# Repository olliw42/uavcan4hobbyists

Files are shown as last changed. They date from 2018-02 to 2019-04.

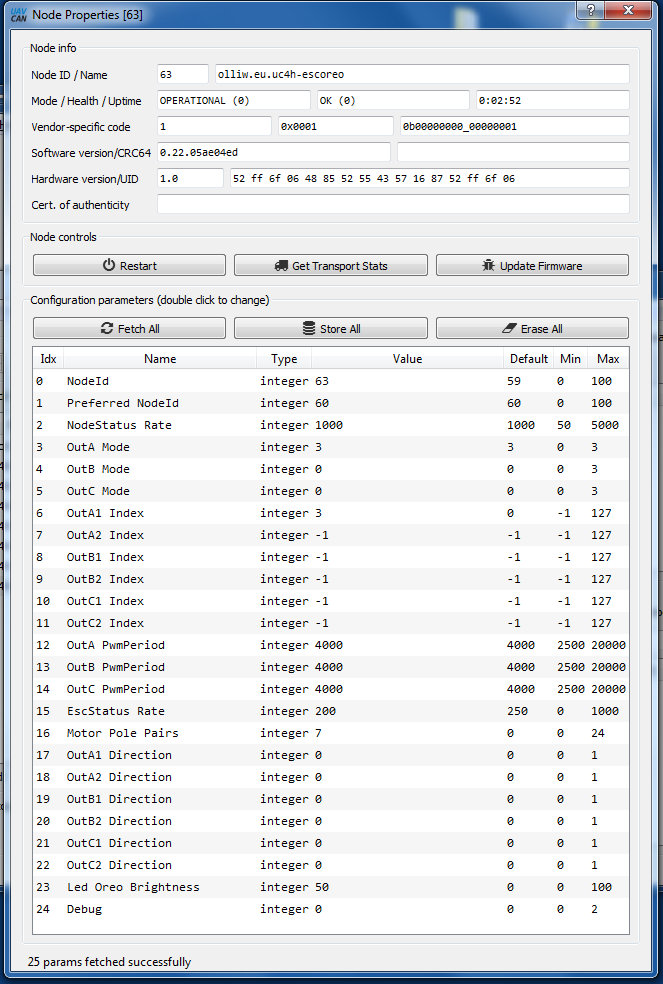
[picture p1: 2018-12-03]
olliws-parameters/olliws-20181203-esc-4.jpg

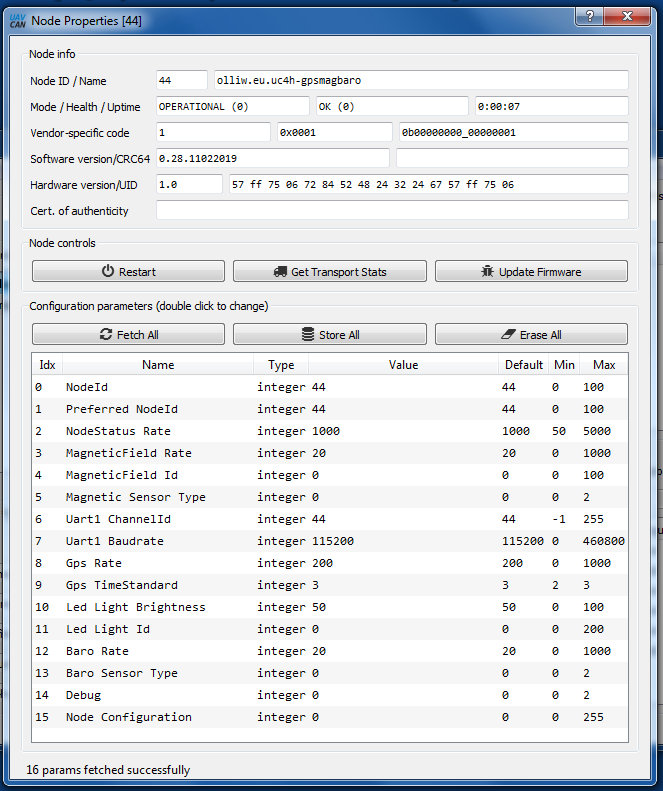
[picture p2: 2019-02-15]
firmware binaries/parameter-screenshoots/uc4h-gps-mag-baro-v028-params.jpg

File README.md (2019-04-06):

# UAVCAN For Hobbyists (UC4H)

The project aims at bringing UAVCAN devices to hobbyists at low cost.

Project web page http://www.olliw.eu/2017/uavcan-for-hobbyists/<br>
Project blog http://www.olliw.eu/2018/uavcan-for-hobbyists-blog/

This project comprises these UAVCAN nodes and devices:

<strong>UC4H GPS-Magnetometer-Barometer Node</strong><br>

<strong>UC4H PowerBrick Node</strong><br>

<strong>UC4H ESC-Actuator Node</strong><br>

<strong>UC4H RangeFinder Node</strong><br>

<strong>UC4H Display Node</strong><br>

<strong>UC4H Notify Node</strong><br>

<strong>UC4H OreoLED Node</strong><br>

<strong>UC4H IndicatorLED Node</strong><br>

<strong>UC4H UartBridge Node</strong><br>

<strong>UC4H Air/Airspeed Node</strong><br>

<strong>UC4H FunThing Node</strong><br>

<strong>UC4H MavlinkBridge</strong><br>

<strong>UC4H SLCAN Adapter</strong><br>

<strong>UC4H Cube Carrier</strong><br>

## TERMS OF USAGE / LICENCE

The material provided in the UC4H Github repository is subject to the following conditions. 

Firmware files: All firmwares are free (but not open source). Besides unlimited private use you are also granted the permission to use them for commercial purposes under the condition that (1) you don’t modify the firmware, e.g. remove or change copyright statements, (2) provide it for free, i.e. don’t charge any explicit or implicit fees to your customers, and (3) correctly and clearly cite the origin of the firmware and the project web page in any product documentation or web page. 

Hardware files: All hardware, for which material is provided, is open source hardware, under the terms of the TAPR Open Hardware License as published by the Free Hardware Foundation, see http://www.tapr.org/ohl.html. The TAPR license explicitly permits essentially unlimited commercial use, with only few conditions such as that copyright logos are not removed.

## ACKNOWLEDGMENTS

The UC4H firmwares make use of Libcanard: https://github.com/UAVCAN/libcanard .
Many thanks to the UAVCAN team, and Pavel Kirienko especially, the main author of Libcanard.

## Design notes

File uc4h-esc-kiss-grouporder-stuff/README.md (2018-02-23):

# UAVCAN For Hobbyists (UC4H)

This is the material for the community group order of assembled UC4H ESC KISS carrier boards. 
See: https://www.rcgroups.com/forums/showthread.php?2869828-Uavcan-for-Hobbyists/page11&perpage=50#post39225194

Please double check if you like, and rport detected issues back in the thread.

:)

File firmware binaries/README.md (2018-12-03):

# UAVCAN For Hobbyists (UC4H)

Project web page http://www.olliw.eu/2017/uavcan-for-hobbyists/<br>
Project blog http://www.olliw.eu/2018/uavcan-for-hobbyists-blog/

## Fimwares ##

Files with a "-4bl" in their name require the UC4H bootloader to be installed. Install procedure:

* Flash the bootloader using e.g. a ST-Link and the SWD pins or a USB-TLL adapter and the system bootloader. It is recommended to also do a full erase.

* Upgrade the firmware via UAVCAN, e.g., by using the UAVCAN GUI Tool.

## Downloading ##

For downloading a single file from a github repo, this appears to be the correct sequence of steps (from https://stackoverflow.com/questions/4604663/download-single-files-from-github):

1. Click the file you want to download to view its content.
2. Click the Raw button.
3. Right-click the mouse and choose Save as.

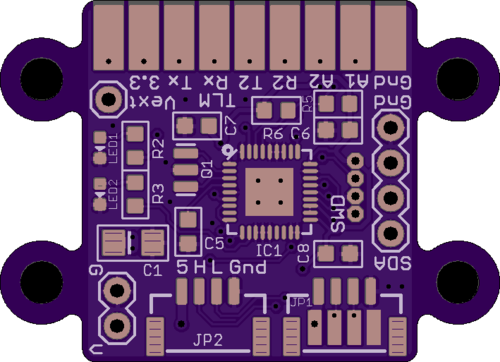
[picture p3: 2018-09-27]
pcbs/UC4H General Purpose Node 2nd Generation/uc4h-node-v2100-oshp-top.png

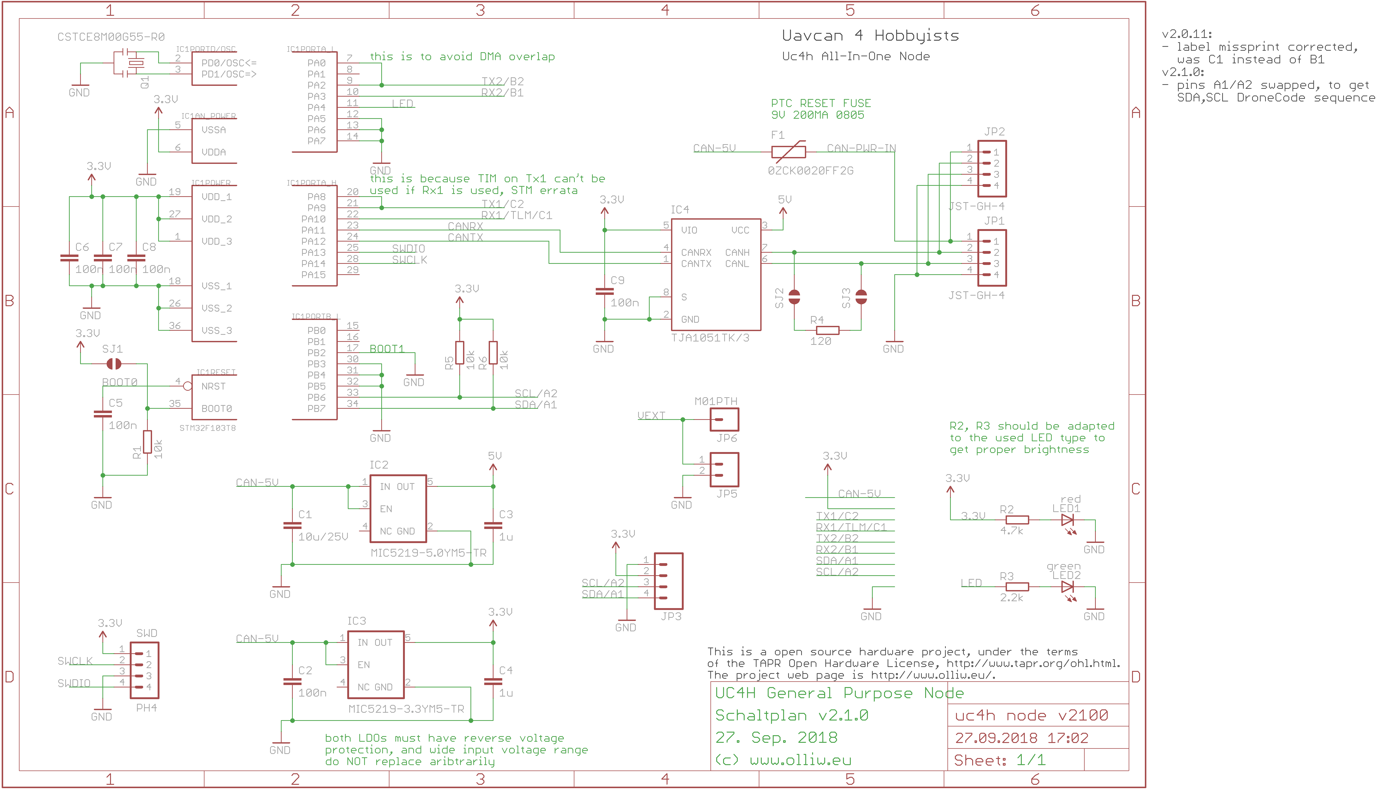
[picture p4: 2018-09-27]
pcbs/UC4H General Purpose Node 2nd Generation/uc4h-node-v2100-scheme.png

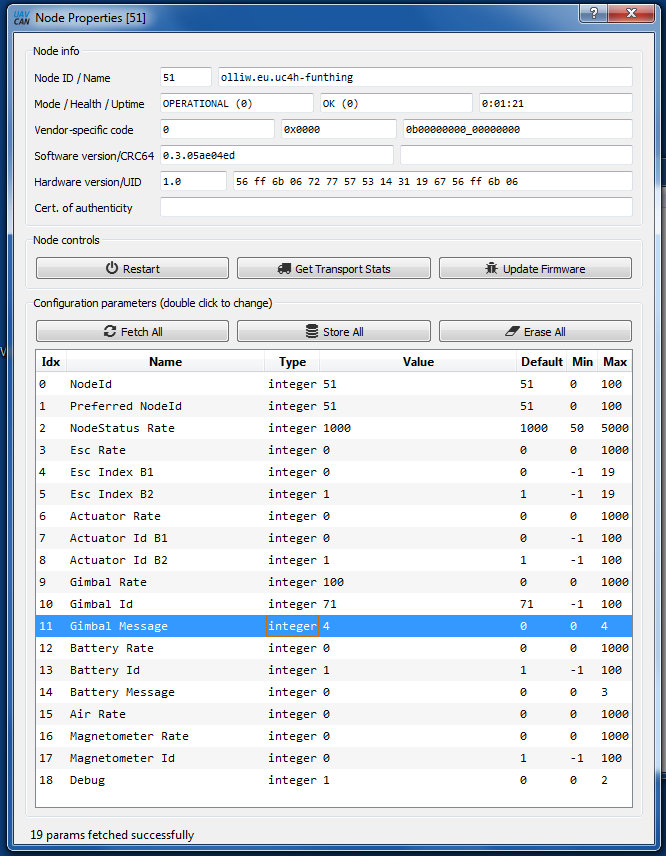
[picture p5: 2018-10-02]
firmware binaries/upto-betacopter36dev-v011/parameter-screenshots/uc4h-funthing-v003-params.jpg

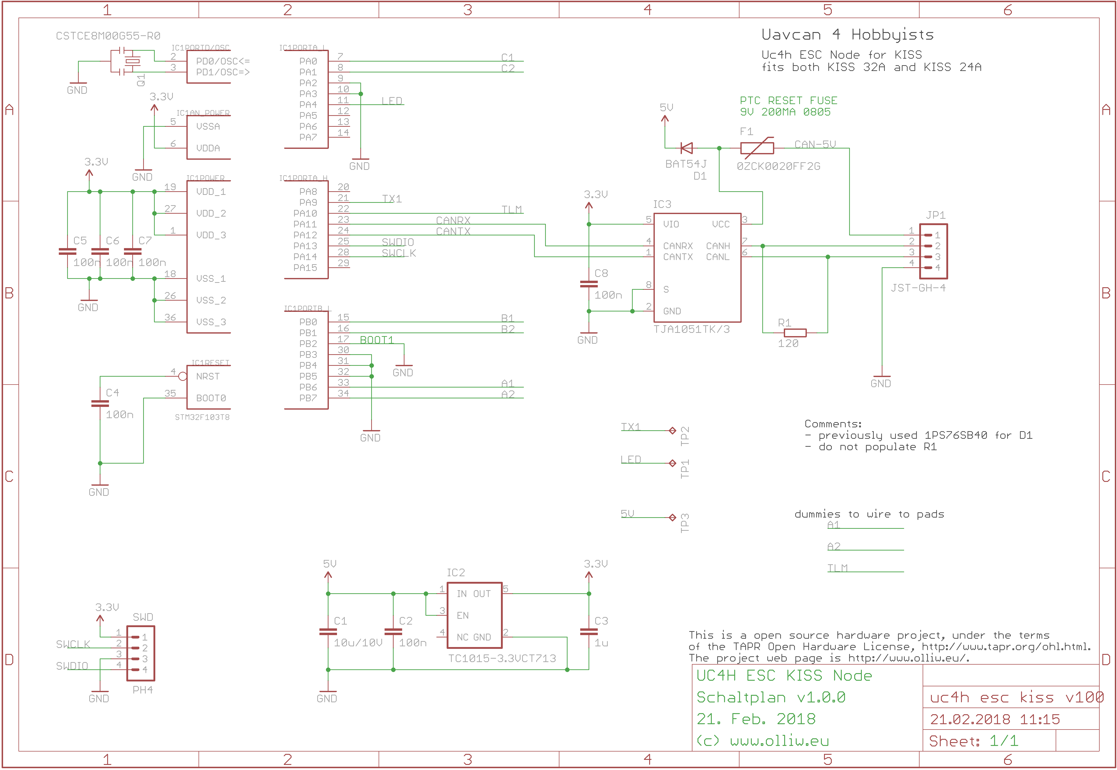
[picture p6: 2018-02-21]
pcbs/UC4H ESC KISS Carrier/uc4h esc kiss v100 scheme.png

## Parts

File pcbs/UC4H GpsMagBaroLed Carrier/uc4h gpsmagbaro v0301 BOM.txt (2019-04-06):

Stückliste exportiert aus C:/Users/Olli/Documents/GitHub/uavcan4hobbyists/pcbs/UC4H GpsMagBaroLed Carrier/uc4h gpsmagbaro v0301.sch am 06.04.2019 08:56

Part Value             Device                Package            Description                                           
C1   10u/25V           C-EUC1206             C1206              CAPACITOR, European symbol                            
C2   100n              C-EUC0603K            C0603K             CAPACITOR, European symbol                            
C3   1u                C-EUC0603K            C0603K             CAPACITOR, European symbol                            
C4   1u                C-EUC0603K            C0603K             CAPACITOR, European symbol                            
C5   100n              C-EUC0603K            C0603K             CAPACITOR, European symbol                            
C6   100n              C-EUC0603K            C0603K             CAPACITOR, European symbol                            
C7   100n              C-EUC0603K            C0603K             CAPACITOR, European symbol                            
C8   100n              C-EUC0603K            C0603K             CAPACITOR, European symbol                            
C9   100n              C-EUC0603K            C0603K             CAPACITOR, European symbol                            
C10  100n              C-EUC0603             C0603              CAPACITOR, European symbol                            
C11  100n              C-EUC0603             C0603              CAPACITOR, European symbol                            
C12  100n              C-EUC0603             C0603              CAPACITOR, European symbol                            
C13  4.7u              C-EUC0805             C0805              CAPACITOR, European symbol                            
C14  220n              C-EUC0603             C0603              CAPACITOR, European symbol                            
C15  100n              C-EUC0603             C0603              CAPACITOR, European symbol                            
C16  100n              C-EUC0603             C0603              CAPACITOR, European symbol                            
C17  100n              C-EUC0603             C0603              CAPACITOR, European symbol                            
C18  100n              C-EUC0603             C0603              CAPACITOR, European symbol                            
C19  100n              C-EUC0603             C0603              CAPACITOR, European symbol                            
C20  100n              C-EUC0603             C0603              CAPACITOR, European symbol                            
F1   0ZCK0020FF2G      FUSE-PTCFUSE-0805     FUSE-0805                                                                
IC1  F103CB            STM32F10XCXT6         TQFP48             ST STM32F101/103 48pin LQFP                           
IC2  MIC5219-5.0YM5-TR V_REG_TPS76433SOT23-5 SOT23-5            Voltage Regulator                                     
IC3  MIC5219-3.3YM5-TR V_REG_TPS76433SOT23-5 SOT23-5            Voltage Regulator                                     
IC4  TJA1051TK/3       TJA1051TK/3           HVSON8                                                                   
IC5  BMP280            BMP280                BMP280             The BMP280 is an absolute barometric pressure sensor. 
IC6  HMC5883LSMD       HMC5883LSMD           16LPCC             3 Axis Digital Compass IC                             
JP1  JST-GH-4TOP-ENTRY JST-GH-4TOP-ENTRY     BM04B-GHS-TBT                                                            
JP2  JST-GH-4TOP-ENTRY JST-GH-4TOP-ENTRY     BM04B-GHS-TBT                                                            
LED1 red               LEDCHIPLED_0603       CHIPLED_0603       LED                                                   
Q1   CSTCE8M00G55-R0   RESONATORSMD          RESONATOR-SMD      Resonator                                             
R1   4.7k              R-EU_R0603            R0603              RESISTOR, European symbol                             
R2   120               R-EU_R0603            R0603              RESISTOR, European symbol                             
R3   10k               R-EU_R0603            R0603              RESISTOR, European symbol                             
R4   10k               R-EU_R0603            R0603              RESISTOR, European symbol                             
SJ1  SOLDERJUMPERNO    SOLDERJUMPERNO        SJ_2S-NO           Solder Jumper                                         
SJ2  SOLDERJUMPERNO    SOLDERJUMPERNO        SJ_2S-NO           Solder Jumper                                         
SJ3  SOLDERJUMPERNO    SOLDERJUMPERNO        SJ_2S-NO           Solder Jumper                                         
SJ4  SOLDERJUMPERNO    SOLDERJUMPERNO        SJ_2S-NO           Solder Jumper                                         
SWD  PH4               P4X1_1P27-OCT_BILEX   4X1_1P27_OCT_BILEX

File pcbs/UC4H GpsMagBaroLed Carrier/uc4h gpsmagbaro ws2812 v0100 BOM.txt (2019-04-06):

Stückliste exportiert aus C:/Users/Olli/Documents/GitHub/uavcan4hobbyists/pcbs/UC4H GpsMagBaroLed Carrier/uc4h gpsmagbaro ws2812 v0100.sch am 06.04.2019 08:57

Part Value   Device    Package Description                
C2   100n    C-EUC0402 C0402   CAPACITOR, European symbol 
JP1          M05PTH    1X05    Header 5                   
LED1 WS2812B WS2812B   WS2812B Features and Benefits

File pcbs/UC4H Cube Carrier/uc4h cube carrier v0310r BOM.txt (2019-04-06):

Stückliste exportiert aus C:/Users/Olli/Documents/GitHub/uavcan4hobbyists/pcbs/UC4H Cube Carrier/uc4h cube carrier v0310r.sch am 06.04.2019 08:51

Part Value                Device                 Package                           Description                          BOM
C1   10u/10V              CPOL-EUSMCA            SMC_A                             POLARIZED CAPACITOR, European symbol    
C2   100n                 C-EUC0603              C0603                             CAPACITOR, European symbol              
C3   100n                 C-EUC0603              C0603                             CAPACITOR, European symbol              
C4   1u                   C-EUC0603              C0603                             CAPACITOR, European symbol              
C5   100n                 C-EUC0603              C0603                             CAPACITOR, European symbol              
C6   100n                 C-EUC0603              C0603                             CAPACITOR, European symbol              
C7   100n                 C-EUC0402              C0402                             CAPACITOR, European symbol              
C8   100n                 C-EUC0603              C0603                             CAPACITOR, European symbol              
C9   100n                 C-EUC0603              C0603                             CAPACITOR, European symbol              
C10  100n                 C-EUC0603              C0603                             CAPACITOR, European symbol              
C11  100n                 C-EUC0603              C0603                             CAPACITOR, European symbol              
C12  100n                 C-EUC0603              C0603                             CAPACITOR, European symbol              
C13  100n                 C-EUC0603              C0603                             CAPACITOR, European symbol              
D1   PMEG3010ER           DIODE-SCHOTTKYSOD123-W SOD123W-DIODE                                                             
D2   BAT54J               DIODE-SOD110-R         SOD110-R                          DIODE                                   
IC1  MAX40200             V_REG_TPS76433SOT23-5  SOT23-5                           Voltage Regulator                       
IC2  TC1185-3.3VCT713     V_REG_TPS76433SOT23-5  SOT23-5                           Voltage Regulator                       
JP1  DF17(1.0H)-80DP-0.5V PIX-CUBE-VIA           PIX-CUBE-DF17(1.0H)-80DP-0.5V-VIA                                         
JP2  USB                  JST-GH-4TOP-ENTRY      BM04B-GHS-TBT                                                             
JP3  SPK                  B3B-ZR                 B3B-ZR                            JST-ZH Connector                        
JP4  CAN1                 JST-GH-4TOP-ENTRY      BM04B-GHS-TBT                                                             
JP5  CAN2                 JST-GH-4TOP-ENTRY      BM04B-GHS-TBT                                                             
JP6  SERIAL1              JST-GH-6TOP-ENTRY      BM06B-GHS-TBT                                                             
JP7  SERIAL2              PINHEAD_4X1            PINHEAD_4X1                                                               
JP8  SERIAL3              PINHEAD_4X1            PINHEAD_4X1                                                               
JP9  SERIAL4              PINHEAD_4X1            PINHEAD_4X1                                                               
JP10 SERIAL5              PINHEAD_4X1            PINHEAD_4X1                                                               
PH1  VDD-BRICK            M02PTH                 1X02                              Header 2                                
PH2  SBUS                 PINHEAD_3X2            PINHEAD_3X2                                                               
PH3  SAFEBUZ              PINHEAD_3X2            PINHEAD_3X2                                                               
PH4  CAN-HIPWR1           M01PTH                 1X01                              Header 1                                
PH5  CAN-HIPWR2           M01PTH                 1X01                              Header 1                                
PH6  SWD                  P4X1_1P27-OCT_BILEX    4X1_1P27_OCT_BILEX                                                        
PH7  SWD2                 P4X1_1P27-OCT_BILEX    4X1_1P27_OCT_BILEX                                                        
R1   10k                  R-EU_R0402             R0402                             RESISTOR, European symbol               
R2   10k                  R-EU_R0402             R0402                             RESISTOR, European symbol               
R3   10k                  R-EU_R0402             R0402                             RESISTOR, European symbol               
R4   470                  R-EU_R0402             R0402                             RESISTOR, European symbol               
SH1  SHORT-HT5            SHORT-HT5              SHORT_TOP-50                      Short between two nets               no 
SH2  SHORT-HT5            SHORT-HT5              SHORT_TOP-50                      Short between two nets               no 
SH3  SHORT-HT5            SHORT-HT5              SHORT_TOP-50                      Short between two nets               no 
SJ1  PWR                  SJ-2WAY-WPASTECONNECT  SJ-2WAY-BIG-WPASTEC                                                       
SJ2  PWR                  SJ-2WAY-STANDARD       SJ-2WAY-BIG                                                               
SJ3  PWR                  SJ-2WAY-WPASTECONNECT  SJ-2WAY-BIG-WPASTEC                                                       
SJ4  SJ-3WAY-03           SJ-3WAY-03             SJ-3WAY-WPASTEC                                                           
T1   FET-NSOT23           FET-NSOT23             SOT23

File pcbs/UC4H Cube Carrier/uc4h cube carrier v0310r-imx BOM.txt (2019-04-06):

Stückliste exportiert aus C:/Users/Olli/Documents/GitHub/uavcan4hobbyists/pcbs/UC4H Cube Carrier/uc4h cube carrier v0310r-imx.sch am 06.04.2019 08:52

Part Value                Device                 Package                           Description                          BOM
C1   10u/10V              CPOL-EUSMCA            SMC_A                             POLARIZED CAPACITOR, European symbol    
C2   100n                 C-EUC0603              C0603                             CAPACITOR, European symbol              
C3   100n                 C-EUC0603              C0603                             CAPACITOR, European symbol              
C4   1u                   C-EUC0603              C0603                             CAPACITOR, European symbol              
C5   100n                 C-EUC0603              C0603                             CAPACITOR, European symbol              
C6   100n                 C-EUC0603              C0603                             CAPACITOR, European symbol              
C7   100n                 C-EUC0402              C0402                             CAPACITOR, European symbol              
C8   100n                 C-EUC0603              C0603                             CAPACITOR, European symbol              
C9   100n                 C-EUC0603              C0603                             CAPACITOR, European symbol              
C10  100n                 C-EUC0603              C0603                             CAPACITOR, European symbol              
C11  100n                 C-EUC0603              C0603                             CAPACITOR, European symbol              
C12  100n                 C-EUC0603              C0603                             CAPACITOR, European symbol              
C13  100n                 C-EUC0603              C0603                             CAPACITOR, European symbol              
C14  100n                 C-EUC0603              C0603                             CAPACITOR, European symbol              
D1   PMEG3010ER           DIODE-SCHOTTKYSOD123-W SOD123W-DIODE                                                             
D2   BAT54J               DIODE-SOD110-R         SOD110-R                          DIODE                                   
IC1  MAX40200             V_REG_TPS76433SOT23-5  SOT23-5                           Voltage Regulator                       
IC2  TC1185-3.3VCT713     V_REG_TPS76433SOT23-5  SOT23-5                           Voltage Regulator                       
JP1  DF17(1.0H)-80DP-0.5V PIX-CUBE-VIA           PIX-CUBE-DF17(1.0H)-80DP-0.5V-VIA                                         
JP2  USB                  JST-GH-4TOP-ENTRY      BM04B-GHS-TBT                                                             
JP3  SPK                  B3B-ZR                 B3B-ZR                            JST-ZH Connector                        
JP4  CAN1                 JST-GH-4TOP-ENTRY      BM04B-GHS-TBT                                                             
JP5  CAN2                 JST-GH-4TOP-ENTRY      BM04B-GHS-TBT                                                             
JP6  SERIAL1              JST-GH-6TOP-ENTRY      BM06B-GHS-TBT                                                             
JP7  SERIAL2              PINHEAD_4X1            PINHEAD_4X1                                                               
JP8  SERIAL3              PINHEAD_4X1            PINHEAD_4X1                                                               
JP9  SERIAL4              PINHEAD_4X1            PINHEAD_4X1                                                               
JP10 SERIAL5              PINHEAD_4X1            PINHEAD_4X1                                                               
PH1  VDD-BRICK            M02PTH                 1X02                              Header 2                                
PH2  SBUS                 PINHEAD_3X2            PINHEAD_3X2                                                               
PH3  SAFEBUZ              PINHEAD_3X2            PINHEAD_3X2                                                               
PH4  CAN-HIPWR1           M01PTH                 1X01                              Header 1                                
PH5  CAN-HIPWR2           M01PTH                 1X01                              Header 1                                
PH6  SWD                  P4X1_1P27-OCT_BILEX    4X1_1P27_OCT_BILEX                                                        
PH7  SWD2                 P4X1_1P27-OCT_BILEX    4X1_1P27_OCT_BILEX                                                        
PH8  VDD-IMX6             M02PTH                 1X02                              Header 2                                
R1   10k                  R-EU_R0402             R0402                             RESISTOR, European symbol               
R2   10k                  R-EU_R0402             R0402                             RESISTOR, European symbol               
R3   10k                  R-EU_R0402             R0402                             RESISTOR, European symbol               
R4   470                  R-EU_R0402             R0402                             RESISTOR, European symbol               
SH1  SHORT-HT5            SHORT-HT5              SHORT_TOP-50                      Short between two nets               no 
SH2  SHORT-HT5            SHORT-HT5              SHORT_TOP-50                      Short between two nets               no 
SH3  SHORT-HT5            SHORT-HT5              SHORT_TOP-50                      Short between two nets               no 
SJ1  PWR                  SJ-2WAY-WPASTECONNECT  SJ-2WAY-BIG-WPASTEC                                                       
SJ2  PWR                  SJ-2WAY-STANDARD       SJ-2WAY-BIG                                                               
SJ3  PWR                  SJ-2WAY-WPASTECONNECT  SJ-2WAY-BIG-WPASTEC                                                       
SJ4  SJ-3WAY-03           SJ-3WAY-03             SJ-3WAY-WPASTEC                                                           
T1   FET-NSOT23           FET-NSOT23             SOT23                                                                     
U$1  PIX-IMX6             PIX-IMX6               PIX-IMX6

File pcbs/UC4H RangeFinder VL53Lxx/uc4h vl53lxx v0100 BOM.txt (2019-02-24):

Stückliste exportiert aus C:/Users/Olli/Documents/Elektronik/Eagle/Uavcan4Hobby/uc4h vl53lxx v0100.sch am 24.02.2019 06:43

Part Value             Device                Package            Description                  
C1   10u/25V           C-EUC1206             C1206              CAPACITOR, European symbol   
C2   100n              C-EUC0603K            C0603K             CAPACITOR, European symbol   
C4   1u                C-EUC0603K            C0603K             CAPACITOR, European symbol   
C5   100n              C-EUC0402             C0402              CAPACITOR, European symbol   
C6   100n              C-EUC0402             C0402              CAPACITOR, European symbol   
C7   100n              C-EUC0402             C0402              CAPACITOR, European symbol   
C8   100n              C-EUC0402             C0402              CAPACITOR, European symbol   
C9   100n              C-EUC0402             C0402              CAPACITOR, European symbol   
C10  100n              C-EUC0402             C0402              CAPACITOR, European symbol   
C11  4.7u              C-EUC0603K            C0603K             CAPACITOR, European symbol   
F1   0ZCK0020FF2G      FUSE-PTCFUSE-0805     FUSE-0805                                       
IC1  STM32F103T8       STM32F10XTXU6         VFQFPN36           STM32F101/103 36pad VFQPFN36 
IC2  MIC5219-3.3YM5-TR V_REG_TPS76433SOT23-5 SOT23-5            Voltage Regulator            
IC4  MAX3051           MAX3051               SOT23-8                                         
IC5  VL53LXX           VL53LXX               VL53LXX                                         
JP1  JST-GH-4          JST-GH-4              SM04B-GHS-TB                                    
JP2  JST-GH-4          JST-GH-4              SM04B-GHS-TB                                    
LED2 green             LEDCHIPLED_0603       CHIPLED_0603       LED                          
Q1   CSTCE8M00G55-R0   RESONATORSMD          RESONATOR-SMD      Resonator                    
R3   2.2k              R-EU_R0402            R0402              RESISTOR, European symbol    
R4   120               R-EU_R0402            R0402              RESISTOR, European symbol    
R5   4.7k              R-EU_R0402            R0402              RESISTOR, European symbol    
R6   4.7k              R-EU_R0402            R0402              RESISTOR, European symbol    
R7   10k               R-EU_R0402            R0402              RESISTOR, European symbol    
SJ1                    SOLDERJUMPERNO        SJ_2S-NO           Solder Jumper                
SWD  PH4               P4X1_1P27-OCT_BILEX   4X1_1P27_OCT_BILEX

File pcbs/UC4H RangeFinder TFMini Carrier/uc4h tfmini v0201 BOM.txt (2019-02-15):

Stückliste exportiert aus C:/Users/Olli/Documents/GitHub/uavcan4hobbyists/pcbs/UC4H RangeFinder TFMini/uc4h tfmini v0201.sch am 15.02.2019 11:02

Part Value             Device                Package            Description                  
C1   10u/25V           C-EUC1206             C1206              CAPACITOR, European symbol   
C2   100n              C-EUC0603K            C0603K             CAPACITOR, European symbol   
C3   1u                C-EUC0603K            C0603K             CAPACITOR, European symbol   
C4   1u                C-EUC0603K            C0603K             CAPACITOR, European symbol   
C5   100n              C-EUC0603K            C0603K             CAPACITOR, European symbol   
C6   100n              C-EUC0603K            C0603K             CAPACITOR, European symbol   
C7   100n              C-EUC0603K            C0603K             CAPACITOR, European symbol   
C8   100n              C-EUC0603K            C0603K             CAPACITOR, European symbol   
C9   100n              C-EUC0603K            C0603K             CAPACITOR, European symbol   
F1   0ZCK0020FF2G      FUSE-PTCFUSE-0805     FUSE-0805                                       
IC1  STM32F103T8       STM32F10XTXU6         VFQFPN36           STM32F101/103 36pad VFQPFN36 
IC2  MIC5219-5.0YM5-TR V_REG_TPS76433SOT23-5 SOT23-5            Voltage Regulator            
IC3  MIC5219-3.3YM5-TR V_REG_TPS76433SOT23-5 SOT23-5            Voltage Regulator            
IC4  TJA1051TK/3       TJA1051TK/3           HVSON8                                          
JP1  JST-GH-4          JST-GH-4              SM04B-GHS-TB                                    
JP2  JST-GH-4          JST-GH-4              SM04B-GHS-TB                                    
Q1   CSTCE8M00G55-R0   RESONATORSMD          RESONATOR-SMD      Resonator                    
R4   120               R-EU_R0603            R0603              RESISTOR, European symbol    
SJ1                    SOLDERJUMPERNO        SJ_2S-NO           Solder Jumper                
SJ2                    SOLDERJUMPERNO        SJ_2S-NO           Solder Jumper                
SWD  PH4               P4X1_1P27-OCT_BILEX   4X1_1P27_OCT_BILEX                              
SWD1 PH4               P4X1_1P27-OCT_BILEX   4X1_1P27_OCT_BILEX

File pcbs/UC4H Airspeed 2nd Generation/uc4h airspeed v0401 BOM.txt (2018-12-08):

Stückliste exportiert aus C:/Users/Olli/Documents/Elektronik/Eagle/Uavcan4Hobby/uc4h airspeed v0401.sch am 08.12.2018 23:26

Part Value             Device                Package            Description                  TP_SIGNAL_NAME
C1   10u/20V           C-EUC1206             C1206              CAPACITOR, European symbol                 
C2   100n              C-EUC0603K            C0603K             CAPACITOR, European symbol                 
C3   1u                C-EUC0603K            C0603K             CAPACITOR, European symbol                 
C4   1u                C-EUC0603K            C0603K             CAPACITOR, European symbol                 
C5   100n              C-EUC0603K            C0603K             CAPACITOR, European symbol                 
C6   100n              C-EUC0603K            C0603K             CAPACITOR, European symbol                 
C7   100n              C-EUC0603K            C0603K             CAPACITOR, European symbol                 
C8   100n              C-EUC0603K            C0603K             CAPACITOR, European symbol                 
C9   100n              C-EUC0603K            C0603K             CAPACITOR, European symbol                 
C10  10u/10V           C-EUC1206             C1206              CAPACITOR, European symbol                 
C11  100n              C-EUC0603K            C0603K             CAPACITOR, European symbol                 
C12  100n              C-EUC0603K            C0603K             CAPACITOR, European symbol                 
D1   BAT54J            DIODE-SOD110-R        SOD110-R           DIODE                                      
F1   0ZCK0020FF2G      FUSE-PTCFUSE-0805     FUSE-0805                                                     
IC1  STM32F103T8       STM32F10XTXU6         VFQFPN36           STM32F101/103 36pad VFQPFN36               
IC2  MIC5219-5.0YM5-TR V_REG_TPS76433SOT23-5 SOT23-5            Voltage Regulator                          
IC3  MIC5219-3.3YM5-TR V_REG_TPS76433SOT23-5 SOT23-5            Voltage Regulator                          
IC4  TJA1051TK/3       TJA1051TK/3           HVSON8                                                        
IC5  DLHRDLHR-8        DLHRDLHR-8            DLHR-8                                                        
JP1  JST-GH-4          JST-GH-4              SM04B-GHS-TB                                                  
JP2  JST-GH-4          JST-GH-4              SM04B-GHS-TB                                                  
LED1 red               LEDCHIPLED_0603       CHIPLED_0603       LED                                        
LED2 green             LEDCHIPLED_0603       CHIPLED_0603       LED                                        
Q1   CSTCE8M00G55-R0   RESONATORSMD          RESONATOR-SMD      Resonator                                  
R2   4.7k              R-EU_R0603            R0603              RESISTOR, European symbol                  
R3   1k                R-EU_R0603            R0603              RESISTOR, European symbol                  
R4   120               R-EU_R0603            R0603              RESISTOR, European symbol                  
R5   10k               R-EU_R0603            R0603              RESISTOR, European symbol                  
R6   4.7k              R-EU_R0603            R0603              RESISTOR, European symbol                  
R7   10k               R-EU_R0603            R0603              RESISTOR, European symbol                  
R8   10k               R-EU_R0603            R0603              RESISTOR, European symbol                  
SJ2                    SOLDERJUMPERNO        SJ_2S-NO           Solder Jumper                              
SJ3                    SOLDERJUMPERNO        SJ_2S-NO           Solder Jumper                              
SPI1 PINHEAD_3X1       PINHEAD_3X1           PINHEAD_3X1                                                   
SPI2 PINHEAD_7X1       PINHEAD_7X1           PINHEAD_7X1                                                   
SWD  PH4               P4X1_1P27-OCT_BILEX   4X1_1P27_OCT_BILEX                                            
TEMP PINHEAD_3X1       PINHEAD_3X1           PINHEAD_3X1                                                   
TP1  TPB1,27           TPB1,27               B1,27              Test pad                                   
TP2  TPB1,27           TPB1,27               B1,27              Test pad                                   
TP3  TPB1,27           TPB1,27               B1,27              Test pad                                   
TP4  TPB1,27           TPB1,27               B1,27              Test pad                                   
TP5  TPB1,27           TPB1,27               B1,27              Test pad

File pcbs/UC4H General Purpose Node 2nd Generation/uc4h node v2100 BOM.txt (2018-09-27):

Stückliste exportiert aus C:/Users/Olli/Documents/Elektronik/Eagle/Uavcan4Hobby/uc4h node v2100.sch am 27.09.2018 17:06

Part Value             Device                Package            Description                  
C1   10u/25V           C-EUC1206             C1206              CAPACITOR, European symbol   
C2   100n              C-EUC0603K            C0603K             CAPACITOR, European symbol   
C3   1u                C-EUC0603K            C0603K             CAPACITOR, European symbol   
C4   1u                C-EUC0603K            C0603K             CAPACITOR, European symbol   
C5   100n              C-EUC0603K            C0603K             CAPACITOR, European symbol   
C6   100n              C-EUC0603K            C0603K             CAPACITOR, European symbol   
C7   100n              C-EUC0603K            C0603K             CAPACITOR, European symbol   
C8   100n              C-EUC0603K            C0603K             CAPACITOR, European symbol   
C9   100n              C-EUC0603K            C0603K             CAPACITOR, European symbol   
F1   0ZCK0020FF2G      FUSE-PTCFUSE-0805     FUSE-0805                                       
IC1  STM32F103T8       STM32F10XTXU6         VFQFPN36           STM32F101/103 36pad VFQPFN36 
IC2  MIC5219-5.0YM5-TR V_REG_TPS76433SOT23-5 SOT23-5            Voltage Regulator            
IC3  MIC5219-3.3YM5-TR V_REG_TPS76433SOT23-5 SOT23-5            Voltage Regulator            
IC4  TJA1051TK/3       TJA1051TK/3           HVSON8                                          
JP1  JST-GH-4          JST-GH-4              SM04B-GHS-TB                                    
JP2  JST-GH-4          JST-GH-4              SM04B-GHS-TB                                    
JP3                    M04PTH                1X04               Header 4                     
JP5                    M02PTH                1X02               Header 2                     
JP6  M01PTH            M01PTH                1X01               Header 1                     
LED1 red               LEDCHIPLED_0603       CHIPLED_0603       LED                          
LED2 green             LEDCHIPLED_0603       CHIPLED_0603       LED                          
Q1   CSTCE8M00G55-R0   RESONATORSMD          RESONATOR-SMD      Resonator                    
R1   10k               R-EU_R0603            R0603              RESISTOR, European symbol    
R2   4.7k              R-EU_R0603            R0603              RESISTOR, European symbol    
R3   2.2k              R-EU_R0603            R0603              RESISTOR, European symbol    
R4   120               R-EU_R0603            R0603              RESISTOR, European symbol    
R5   10k               R-EU_R0603            R0603              RESISTOR, European symbol    
R6   10k               R-EU_R0603            R0603              RESISTOR, European symbol    
SJ1  BOOT0             SOLDERJUMPERNO        SJ_2S-NO           Solder Jumper                
SJ2                    SOLDERJUMPERNO        SJ_2S-NO           Solder Jumper                
SJ3                    SOLDERJUMPERNO        SJ_2S-NO           Solder Jumper                
SWD  PH4               P4X1_1P27-OCT_BILEX   4X1_1P27_OCT_BILEX

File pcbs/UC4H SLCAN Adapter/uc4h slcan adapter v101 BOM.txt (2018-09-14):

Stückliste exportiert aus C:/Users/Olli/Documents/Elektronik/Eagle/Uavcan4Hobby/uc4h slcan adapter v101.sch am 14.09.2018 20:08

Part       Value                    Device                 Package            Description                  
5V-EXT     PH2                      M02PTH                 1X02               Header 2                     
C1         10u/10V                  C-EUC1206              C1206              CAPACITOR, European symbol   
C2         100n                     C-EUC0603K             C0603K             CAPACITOR, European symbol   
C3         1u                       C-EUC0603K             C0603K             CAPACITOR, European symbol   
C4         100n                     C-EUC0603K             C0603K             CAPACITOR, European symbol   
C5         100n                     C-EUC0603K             C0603K             CAPACITOR, European symbol   
C6         100n                     C-EUC0603K             C0603K             CAPACITOR, European symbol   
C7         100n                     C-EUC0603K             C0603K             CAPACITOR, European symbol   
C8         100n                     C-EUC0603K             C0603K             CAPACITOR, European symbol   
C9         100n                     C-EUC0603K             C0603K             CAPACITOR, European symbol   
C10        4.7u                     C-EUC0805              C0805              CAPACITOR, European symbol   
C11        100n                     C-EUC0603K             C0603K             CAPACITOR, European symbol   
CAN#1      JST-GH-4                 JST-GH-4               SM04B-GHS-TB                                    
CAN#2      JST-GH-4                 JST-GH-4               SM04B-GHS-TB                                    
CAN#3      PH4                      M04PTH                 1X04               Header 4                     
CAN#4      PH4                      M04PTH                 1X04               Header 4                     
CAN-5V-SRC PH2                      M02PTH                 1X02               Header 2                     
CAN-PWR    PH2                      M02PTH                 1X02               Header 2                     
D1         PMEG3010ER               DIODE-SCHOTTKYSOD123-W SOD123W-DIODE                                   
D2         PMEG3010ER               DIODE-SCHOTTKYSOD123-W SOD123W-DIODE                                   
D3         PMEG3010ER               DIODE-SCHOTTKYSOD123-W SOD123W-DIODE                                   
F1         FUSE-PTC                 FUSE-PTC               FUSE-1206                                       
IC1        STM32F103T8              STM32F10XTXU6          VFQFPN36           STM32F101/103 36pad VFQPFN36 
IC2        MIC5219-3.3YM5-TR        V_REG_TPS76433SOT23-5  SOT23-5            Voltage Regulator            
IC3        TJA1051TK/3              TJA1051TK/3            HVSON8                                          
IC4        CP2102N-QFN24            CP2102N-QFN24          QFN24-CP2102N                                   
JP4        PH2                      M02PTH                 1X02               Header 2                     
LED1       red                      LEDCHIPLED_0603        CHIPLED_0603       LED                          
LED2       green                    LEDCHIPLED_0603        CHIPLED_0603       LED                          
LED3       yellow                   LEDCHIPLED_0603        CHIPLED_0603       LED                          
LED4       green                    LEDCHIPLED_0603        CHIPLED_0603       LED                          
LED5       yellow                   LEDCHIPLED_0603        CHIPLED_0603       LED                          
Q1         CSTCE8M00G55-R0          RESONATORSMD           RESONATOR-SMD      Resonator                    
R1         10k                      R-EU_R0603             R0603              RESISTOR, European symbol    
R2         4.7k                     R-EU_R0603             R0603              RESISTOR, European symbol    
R3         2.2k                     R-EU_R0603             R0603              RESISTOR, European symbol    
R4         2.2k                     R-EU_R0603             R0603              RESISTOR, European symbol    
R5         1k                       R-EU_R0603             R0603              RESISTOR, European symbol    
R6         2.2k                     R-EU_R0603             R0603              RESISTOR, European symbol    
R7         2.2k                     R-EU_R0603             R0603              RESISTOR, European symbol    
SJ1        BOOT0                    SOLDERJUMPERNO         SJ_2S-NO           Solder Jumper                
SWD        PH4                      P4X1_1P27-OCT_BILEX    4X1_1P27_OCT_BILEX                              
UART2      PH4                      M04PTH                 1X04               Header 4                     
USB        Amphenol 10118192-0001LF USB-MICROB             USB-MICROB         USB Connectors

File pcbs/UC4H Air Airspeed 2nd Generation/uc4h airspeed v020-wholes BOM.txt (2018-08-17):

Stückliste exportiert aus C:/Users/Olli/Documents/Elektronik/Eagle/Uavcan4Hobby/uc4h airspeed v020-wholes.sch am 17.08.2018 21:32

Part Value             Device                Package            Description                  TP_SIGNAL_NAME
C1   10u/20V           C-EUC1206             C1206              CAPACITOR, European symbol                 
C2   100n              C-EUC0603K            C0603K             CAPACITOR, European symbol                 
C3   1u                C-EUC0603K            C0603K             CAPACITOR, European symbol                 
C4   1u                C-EUC0603K            C0603K             CAPACITOR, European symbol                 
C5   100n              C-EUC0603K            C0603K             CAPACITOR, European symbol                 
C6   100n              C-EUC0603K            C0603K             CAPACITOR, European symbol                 
C7   100n              C-EUC0603K            C0603K             CAPACITOR, European symbol                 
C8   100n              C-EUC0603K            C0603K             CAPACITOR, European symbol                 
C9   100n              C-EUC0603K            C0603K             CAPACITOR, European symbol                 
C10  10u/10V           C-EUC1206             C1206              CAPACITOR, European symbol                 
C11  100n              C-EUC0603K            C0603K             CAPACITOR, European symbol                 
C12  10u/10V           C-EUC1206             C1206              CAPACITOR, European symbol                 
C13  100n              C-EUC0603K            C0603K             CAPACITOR, European symbol                 
D1   BAT54J            DIODE-SOD110-R        SOD110-R           DIODE                                      
F1   0ZCK0020FF2G      FUSE-PTCFUSE-0805     FUSE-0805                                                     
IC1  STM32F103T8       STM32F10XTXU6         VFQFPN36           STM32F101/103 36pad VFQPFN36               
IC2  MIC5219-5.0YM5-TR V_REG_TPS76433SOT23-5 SOT23-5            Voltage Regulator                          
IC3  MIC5219-3.3YM5-TR V_REG_TPS76433SOT23-5 SOT23-5            Voltage Regulator                          
IC4  TJA1051TK/3       TJA1051TK/3           HVSON8                                                        
IC5  HW-RSC            HW-RSC                HONEYWELL-8                                                   
IC6  HW-RSC            HW-RSC                HONEYWELL-8                                                   
JP1  JST-GH-4          JST-GH-4              SM04B-GHS-TB                                                  
JP2  JST-GH-4          JST-GH-4              SM04B-GHS-TB                                                  
JP3  PINHEAD_3X1       PINHEAD_3X1           PINHEAD_3X1                                                   
LED1 red               LEDCHIPLED_0603       CHIPLED_0603       LED                                        
LED2 green             LEDCHIPLED_0603       CHIPLED_0603       LED                                        
Q1   CSTCE8M00G55-R0   RESONATORSMD          RESONATOR-SMD      Resonator                                  
R1   10k               R-EU_R0603            R0603              RESISTOR, European symbol                  
R2   4.7k              R-EU_R0603            R0603              RESISTOR, European symbol                  
R3   1k                R-EU_R0603            R0603              RESISTOR, European symbol                  
R4   120               R-EU_R0603            R0603              RESISTOR, European symbol                  
R5   1k                R-EU_R0603            R0603              RESISTOR, European symbol                  
R6   1k                R-EU_R0603            R0603              RESISTOR, European symbol                  
R7   1k                R-EU_R0603            R0603              RESISTOR, European symbol                  
R8   1k                R-EU_R0603            R0603              RESISTOR, European symbol                  
R9   4.7k              R-EU_R0603            R0603              RESISTOR, European symbol                  
SJ1  BOOT0             SOLDERJUMPERNO        SJ_2S-NO           Solder Jumper                              
SJ2                    SOLDERJUMPERNO        SJ_2S-NO           Solder Jumper                              
SJ3                    SOLDERJUMPERNO        SJ_2S-NO           Solder Jumper                              
SWD  PH4               P4X1_1P27-OCT_BILEX   4X1_1P27_OCT_BILEX                                            
TP1  TPB1,27           TPB1,27               B1,27              Test pad                                   
TP2  TPB1,27           TPB1,27               B1,27              Test pad                                   
TP3  TPB1,27           TPB1,27               B1,27              Test pad                                   
TP4  TPB1,27           TPB1,27               B1,27              Test pad                                   
TP5  TPB1,27           TPB1,27               B1,27              Test pad

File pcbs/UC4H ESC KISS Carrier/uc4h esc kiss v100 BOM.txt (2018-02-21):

Stückliste exportiert aus C:/Users/Olli/Documents/GitHub/uavcan4hobbyists/pcbs/UC4H ESC KISS Carrier/uc4h esc kiss v100.sch am 21.02.2018 11:36

Part Value            Device                Package            Description                  TP_SIGNAL_NAME
C1   10u/10V          C-EUC1206             C1206              CAPACITOR, European symbol                 
C2   100n             C-EUC0603K            C0603K             CAPACITOR, European symbol                 
C3   1u               C-EUC0603K            C0603K             CAPACITOR, European symbol                 
C4   100n             C-EUC0603K            C0603K             CAPACITOR, European symbol                 
C5   100n             C-EUC0603K            C0603K             CAPACITOR, European symbol                 
C6   100n             C-EUC0603K            C0603K             CAPACITOR, European symbol                 
C7   100n             C-EUC0603K            C0603K             CAPACITOR, European symbol                 
C8   100n             C-EUC0603K            C0603K             CAPACITOR, European symbol                 
D1   BAT54J           DIODE-SOD110-R        SOD110-R           DIODE                                      
F1   0ZCK0020FF2G     FUSE-PTCFUSE-0805     FUSE-0805                                                     
IC1  STM32F103T8      STM32F10XTXU6         VFQFPN36           STM32F101/103 36pad VFQPFN36               
IC2  TC1015-3.3VCT713 V_REG_TPS76433SOT23-5 SOT23-5            Voltage Regulator                          
IC3  TJA1051TK/3      TJA1051TK/3           HVSON8                                                        
JP1  JST-GH-4         JST-GH-4              SM04B-GHS-TB                                                  
Q1   CSTCE8M00G55-R0  RESONATORSMD          RESONATOR-SMD      Resonator                                  
R1   120              R-EU_R0603            R0603              RESISTOR, European symbol                  
SWD  PH4              P4X1_1P27-OCT_BILEX   4X1_1P27_OCT_BILEX                                            
TP1  TPB1,27          TPB1,27               B1,27              Test pad                                   
TP2  TPB1,27          TPB1,27               B1,27              Test pad                                   
TP3  TPB1,27          TPB1,27               B1,27              Test pad

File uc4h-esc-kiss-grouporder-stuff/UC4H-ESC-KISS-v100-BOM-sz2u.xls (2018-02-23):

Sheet: Read me
Note:
1. The blue fields must be fulfilled before uploaded. Filling out the BOM Completely will facilitate the quotation.
2. Reference Link from Digikey, Mouser, Farnell,Arrow, Avenet or ShenZhen2U.com is strongly suggested. If the part are available in our shop, please copy the link in the "Reference Link".
3.Component values should be clear e.g. 100R, 100K, 100M etc, and not just "100" printed as the value.
4.BOMs must clearly identify parts are supplied by either "Customer", "SZ2U" or "No Need".
5.If you are going to sourcing and assembling with us,component must be supplied with extra (spare) parts to allow for losses and wastage. 5% extra spares is a reasonable guideline.Surplus parts will be returned.
6.We will respond with your BOM pricing within two to four working days of receiving it.Depending on suppliers responding with pricing for rare or bespoke items,so we cannot give a precise turnaround time for quote.
7.We are not taking any responsibility for your BOM files, please make sure that they are clear and accurate.
Blue fields | Should be filled out by customer.
Green fields | will be calculated and filled autolly.
After fulfilled and checked by yourself,save this file as .xls or .xlsx (not PDF), and send it to pcb@shenzhen2u.com

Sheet: BOM
 |  |  |  | BOM & Assembly Template
 | Custom Name: | Oliver Waldmann |  |  | Project Name: | UC4H ESC KISS v100 |  |  | Sale: | Iver
 | Company Name: | private, www.olliw.eu |  |  | BOM Quantity: |  |  |  | Email: | pcb@shenzhen2u.com
 | Address: | Marchstrasse 25 |  |  |  |  |  |  | Quotation ID:
 |  | D-79211 Denzlingen |  |  |  |  |  |  | Date: | 2018-02-21
 |  | Germany
 | Email: | waldmanns@gmx.de |  |  | Quotation for: | BOM & Assembly |  |  | Currency: | USD
 | Tel:
# | Part ID / Reference | Manufacturer | Manufacture Part Number | Description | Value | Package | Reference Link | Alternate | THT/SMD/ No-Lead Pads | Pins / Pads | Quantity per BOM | Spare (%) | Need Qty | supplied by
1 | C1 | AVX Corporation | TAJA106K010RNJ | Capacitor | 10u/10V | 1206/SMC_A | https://www.digikey.de/product-detail/de/avx-corporation/TAJA106K010RNJ/478-1654-1-ND/564686 | - | SMD | 2 | 1 | 5 | 0 | SZ2U
2 | C2,C4,C5,C6,C7,C8 | KEMET | C0603C104K5RACTU | Capacitor | 100n | 0603 | https://www.digikey.de/product-detail/de/kemet/C0603C104K5RACTU/399-5089-1-ND/1465623 | - | SMD | 2 | 6 | 5 | 5 | SZ2U
3 | C3 | KEMET | C0603C105K3RACTU | Capacitor | 1u | 0603 | https://www.digikey.de/product-detail/de/kemet/C0603C105K3RACTU/399-7376-1-ND/3317410 | - | SMD | 2 | 1 | 5 | 5 | SZ2U
4 | R1 |  |  | Resistor | 120R | 0603 |  | - | SMD |  | 0 | 5 | 5 | No Need
5 | F1 | Bel Fuse Inc. | 0ZCK0020FF2G | Fuse 200mA | 0ZCK0020FF2G | 0805 | https://www.digikey.de/product-detail/de/bel-fuse-inc/0ZCK0020FF2G/507-1811-1-ND/4156251 | - | SMD | 2 | 1 | 5 | 5 | SZ2U
6 | IC1 | STMicroelectronics | STM32F103T8U6 | STM32103T8 | STM32F103T8U6 | VFQFPN36 | https://www.digikey.de/product-detail/de/stmicroelectronics/STM32F103T8U6/497-11532-ND/1852493 | - | No-Lead Pads | 36 | 1 | 5 | 5 | SZ2U
7 | IC2 | Microchip Technology | TC1015-3.3VCT713 | 3.3V LDO | TC1015-3.3VCT713 | SOT23-5 | https://www.digikey.de/product-detail/de/microchip-technology/TC1015-3.3VCT713/TC1015-3.3VCT713CT-ND/1979796 | - | SMD | 5 | 1 | 5 | 5 | SZ2U
8 | IC3 | NXP Semiconductors | TJA1051TK/3,118 | CAN transceiver | TJA1051TK/3 | HVSON8 | https://www.digikey.de/product-detail/de/nxp-usa-inc/TJA1051TK-3118/568-8686-1-ND/2803572 | - | No-Lead Pads | 8 | 1 | 5 | 5 | SZ2U
9 | Q1 | Murata Electronics | CSTCE8M00G55-R0 | Resonator | 8 MHz | 3-SMD, 3.2x1.3 | https://www.digikey.de/product-detail/de/murata-electronics-north-america/CSTCE8M00G55-R0/490-1195-1-ND/584632 | - | SMD | 3 | 1 | 5 | 5 | SZ2U
10 | D1 | Nexperia USA Inc. | BAT54J,115 | Diode | BAT54J | SOD-323F | https://www.digikey.de/product-detail/de/nexperia-usa-inc/BAT54J115/1727-4818-1-ND/2531305 | - | SMD | 2 | 1 | 5 | 5 | SZ2U
11 | JP1 | JST Sales America Inc. | SM04B-GHS-TB(LF)(SN)- | JST-GH-4 | SM04B-GHS-TB | JST-GH-4 | https://www.digikey.de/product-detail/de/jst-sales-america-inc/SM04B-GHS-TB-LF-SN/455-1566-6-ND/1963482 | - | SMD | 6 | 1 | 5 | 5 | SZ2U
12
13
14
15
16
17
18
19
20
21
22
23
24
25
26
27
28
29
30
31
32
33
34
35
36
37
38
39
40
41
42
43
44
45
46
47
48
49
50
51
52
53
54
55
56
57
58
59
60
61
62
63
64
65
66
67
68
69
70
71
72
73
74
75
76
77
78
79
80
81
82
83
84
85
86
87
88
89
90
91
92
93
94
95
96
97
98
99
100
101
102
103
104
105
106
107
108
109
110
111
112
113
114
115
116
117
118
119
120
121
122
123
124
125
126
127
128
129
130
131
132
133
134
135
136
137
138
139
140
141
142
143
144
145
146
147
148
149
150
151
152
153
154
155
156
157
158
159
160
161
162
163
164
165
166
167
168
169
170
171
172
173
174
175
176
177
178
179
180
181
182
183
184
185
186
187
188
189
190
191
192
193
194
195
196
197
198
199
200
201
202
203
204
205
206
207
208
209
210
211
212
213
214
215
216
217
218
219
220
221
222
223
224
225
226
227
228
229
230
231
232
233
234
235
236
237
238
239
240
241
242
243
244
245
246
247
248
249
250
251
252
253
254
255
256
257
258
259
260
261
262
263
264
265
266
267
268
269
270
271
272
273
274
275
276
277
278
279
280
281
282
283
284
285
286
287
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

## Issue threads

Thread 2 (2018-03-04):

3d model for UC4H ESC

j3qq4hch, 2018-03-04:
Hi! I've exported 3d model for your UC4H ESC adapter in its current stage.
It is eagle-to-sketchup, so STEPs are not an option. But this may help if you want to create some 3d-printed mounts or something like that.

Please tell me where to put it.

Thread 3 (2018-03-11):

Hex downloads

auturgy, 2018-03-11:
Not sure of the cause, and it’s most likely the problem is at my end - so this is more a note for users than an ‘issue’.  For me, downloading the latest Hex files directly resulted in file corruption (each of them, I tried a bunch of things). Pulling the repo down as a zip did not have the same error, and the files flashed fine. Win10/Chrome & FF.

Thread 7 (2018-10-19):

SLCAN PROBLEM

skyyuzhang, 2018-10-19:
I have been successful to build slcan adapter and also I can connect it to any modules of UC4H but I cannot connect Sapog ESC . when connect to the adapter the UAVCANGUI doesn't show any node !!!!!why . when I fist meet this problem I think it must be hardware problem . so  I checked Sapog ESC hardware but nothing wrong.  after this I tired to flash U4CH bootloader  in to my Sapog hardware. and  the UAVCANGUI show the node  .  is UC4H Adapter not compatible whit Sapog ESC????  or it just only compatible with UC4H?   Is this a bug?  thanks!!!!!!!

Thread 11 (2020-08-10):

UC4H PowerBrick Board

juvinski, 2020-08-10:
Hi @olliw42

congratz I'm using your uavcan and is amazing.
Any change to publish the power brick board and bom ?

Thanks a lot.

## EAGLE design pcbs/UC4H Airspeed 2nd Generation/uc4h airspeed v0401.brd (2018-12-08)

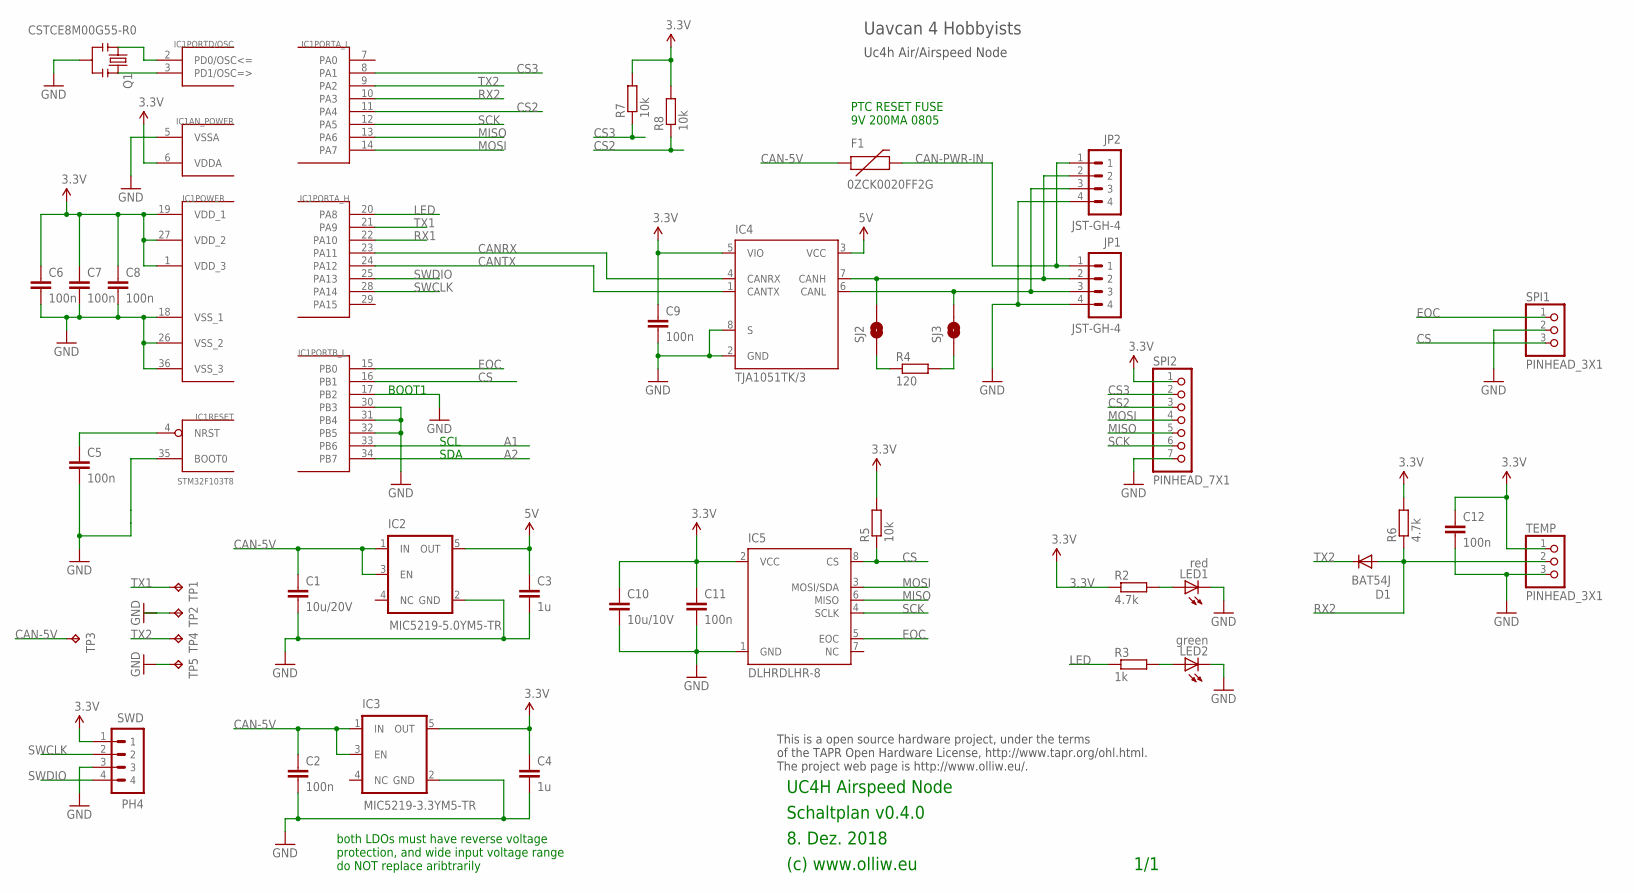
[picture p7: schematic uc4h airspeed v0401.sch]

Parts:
C1: 10u/20V; C1206
C2, C5, C6, C7, C8, C9, C11, C12: 100n; C0603K
C3, C4: 1u; C0603K
C10: 10u/10V; C1206
D1: BAT54J; SOD110-R
F1: 0ZCK0020FF2G; FUSE-0805
IC1: STM32F103T8; VFQFPN36
IC2: MIC5219-5.0YM5-TR; SOT23-5
IC3: MIC5219-3.3YM5-TR; SOT23-5
IC4: TJA1051TK/3; HVSON8
IC5: DLHRDLHR-8; DLHR-8
JP1, JP2: JST-GH-4; SM04B-GHS-TB
LED1: red; CHIPLED_0603
LED2: green; CHIPLED_0603
Q1: CSTCE8M00G55-R0; RESONATOR-SMD
R2, R6: 4.7k; R0603
R3: 1k; R0603
R4: 120; R0603
R5, R7, R8: 10k; R0603
SJ2, SJ3: SOLDERJUMPERNO; SJ_2S-NO
SPI1: PINHEAD_3X1
SPI2: PINHEAD_7X1
SWD: PH4; 4X1_1P27_OCT_BILEX
TEMP: PINHEAD_3X1
TP1, TP2, TP3, TP4, TP5: TPB1,27; B1,27

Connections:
3.3V: C4.1, C6.1, C7.1, C8.1, C9.1, C10.1, C11.1, C12.1, IC1.1 (VDD_3), IC1.6 (VDDA), IC1.19 (VDD_1), IC1.27 (VDD_2), IC3.5 (OUT), IC4.5 (VIO), IC5.2 (VCC), R2.1, R5.2, R6.2, R7.2, R8.2, SPI2.1, SWD.1, TEMP.1
5V: C3.1, IC2.5 (OUT), IC4.3 (VCC)
A1: IC1.33 (PB6)
A2: IC1.34 (PB7)
CAN-5V: C1.1, C2.1, F1.1, IC2.1 (IN), IC2.3 (EN), IC3.1 (IN), IC3.3 (EN), TP3.TP
CAN-PWR-IN: F1.2, JP1.1, JP2.1
CANH: IC4.7 (CANH), JP1.2, JP2.2, SJ2.2
CANL: IC4.6 (CANL), JP1.3, JP2.3, SJ3.2
CANRX: IC1.23 (PA11), IC4.4 (CANRX)
CANTX: IC1.24 (PA12), IC4.1 (CANTX)
CS: IC1.16 (PB1), IC5.8 (CS), R5.1, SPI1.3 (5)
CS2: IC1.11 (PA4), R8.1, SPI2.3
CS3: IC1.8 (PA1), R7.1, SPI2.2
EOC: IC1.15 (PB0), IC5.5 (EOC), SPI1.1
GND: C1.2, C2.2, C3.2, C4.2, C5.2, C6.2, C7.2, C8.2, C9.2, C10.2, C11.2, C12.2, IC1.5 (VSSA), IC1.17 (PB2), IC1.18 (VSS_1), IC1.26 (VSS_2), IC1.30 (PB3), IC1.31 (PB4), IC1.32 (PB5), IC1.35 (BOOT0), IC1.36 (VSS_3), IC2.2 (GND), IC3.2 (GND), IC4.2 (GND), IC4.8 (S), IC5.1 (GND), JP1.4, JP2.4, LED1.C, LED2.C, Q1.2, SPI1.2 (3), SPI2.7, SWD.3, TEMP.3 (5), TP2.TP, TP5.TP
LED: IC1.20 (PA8), R3.1
MISO: IC1.13 (PA6), IC5.6 (MISO), SPI2.5
MOSI: IC1.14 (PA7), IC5.3 (MOSI/SDA), SPI2.4
unnamed: C5.1, IC1.4 (NRST)
unnamed: LED2.A, R3.2
unnamed: R4.1, SJ2.1
unnamed: IC1.2 (PD0/OSC<=), Q1.1
unnamed: IC1.3 (PD1/OSC=>), Q1.3
unnamed: R4.2, SJ3.1
unnamed: LED1.A, R2.2
RX1: IC1.22 (PA10)
RX2: D1.A, IC1.10 (PA3), R6.1, TEMP.2 (3)
SCK: IC1.12 (PA5), IC5.4 (SCLK), SPI2.6
SWCLK: IC1.28 (PA14), SWD.2
SWDIO: IC1.25 (PA13), SWD.4
TX1: IC1.21 (PA9), TP1.TP
TX2: D1.C, IC1.9 (PA2), TP4.TP

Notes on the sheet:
8. Dez. 2018
(c) www.olliw.eu
UC4H Airspeed Node
Schaltplan v0.4.0
This is a open source hardware project, under the terms of the TAPR Open Hardware License, http://www.tapr.org/ohl.html. The project web page is http://www.olliw.eu/.
1/1
Uc4h Air/Airspeed Node
Uavcan 4 Hobbyists
BOOT1
PTC RESET FUSE 9V 200MA 0805
both LDOs must have reverse voltage protection, and wide input voltage range do NOT replace aribtrarily
SCL
SDA

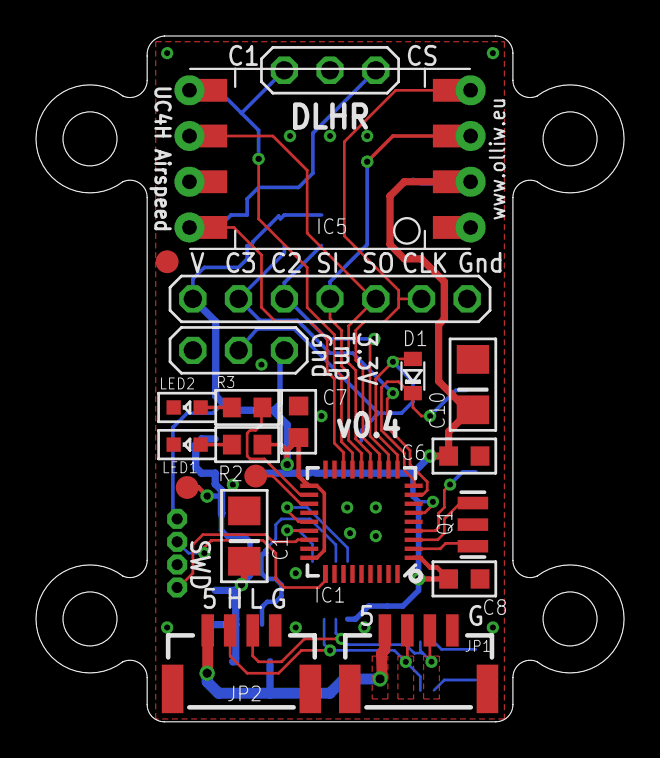
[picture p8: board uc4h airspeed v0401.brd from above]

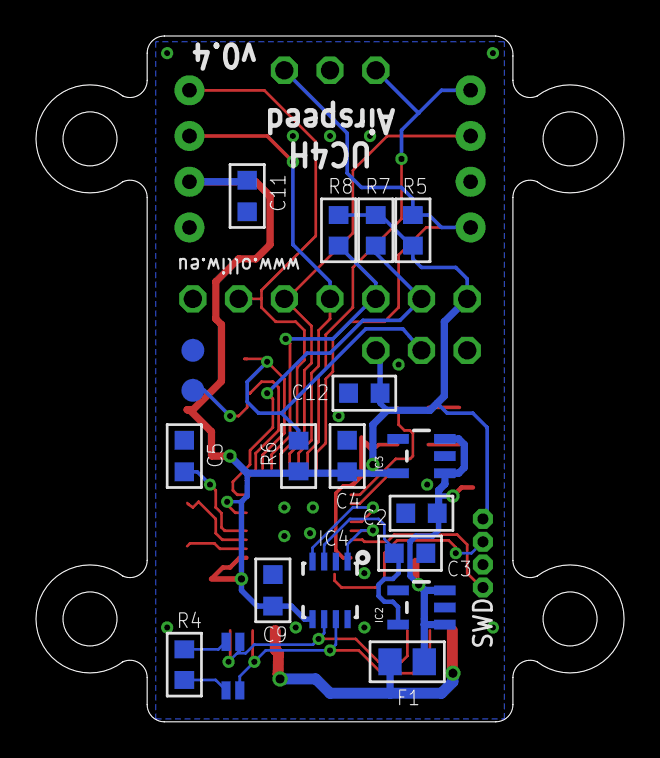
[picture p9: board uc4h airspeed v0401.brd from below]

Board: 2 copper layers, 32.7 x 38.1 mm, 42 parts (20 on the bottom side), 29 nets.

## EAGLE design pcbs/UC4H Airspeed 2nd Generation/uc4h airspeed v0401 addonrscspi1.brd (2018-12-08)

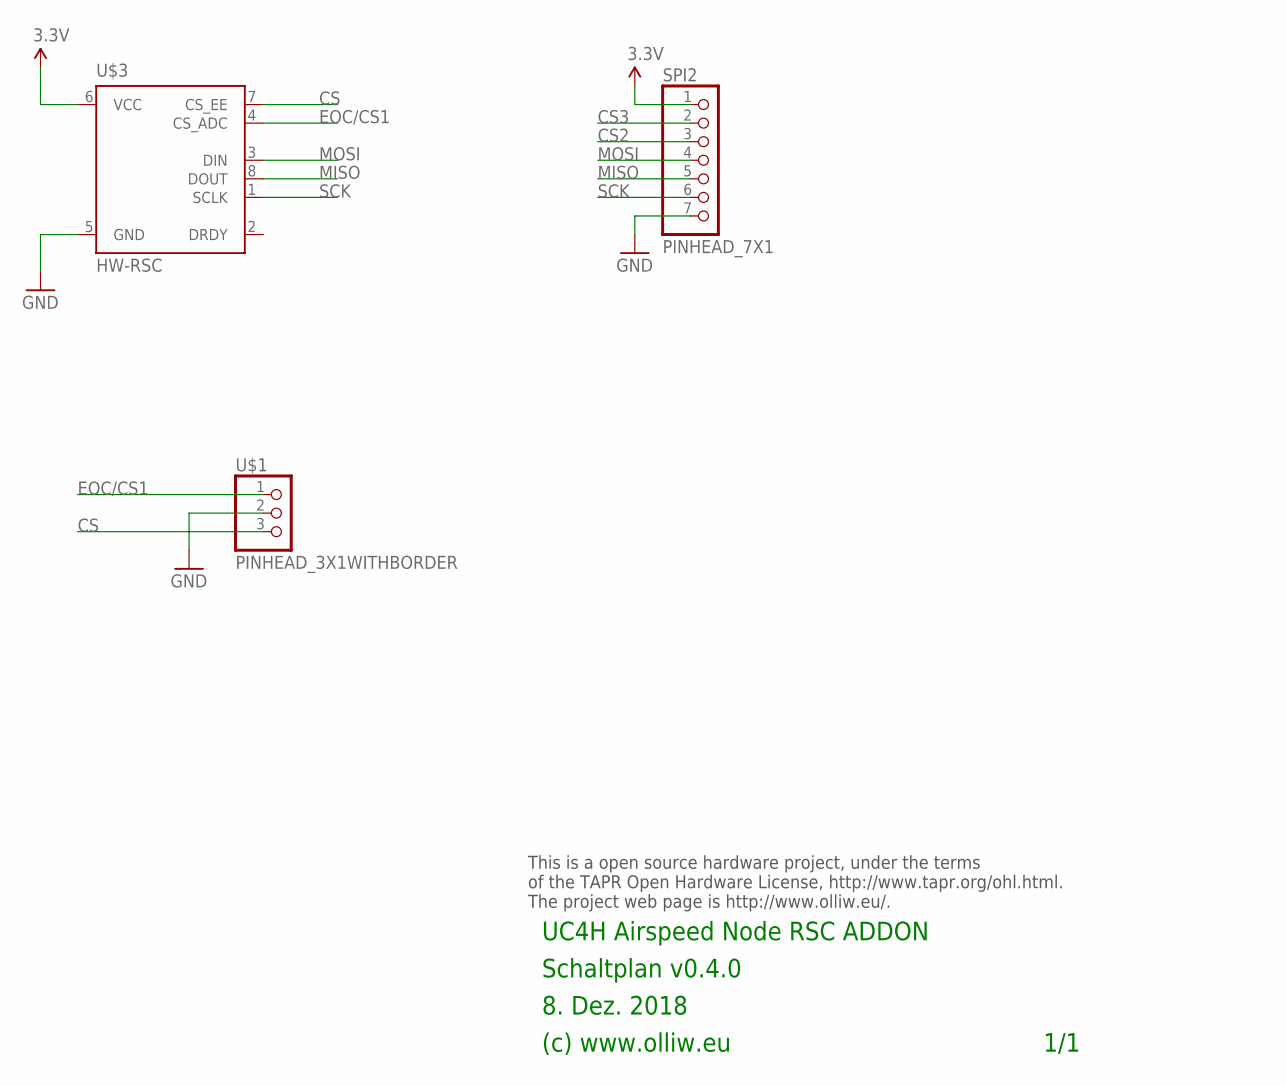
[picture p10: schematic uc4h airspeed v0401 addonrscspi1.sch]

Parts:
SPI2: PINHEAD_7X1
U$1: PINHEAD_3X1WITHBORDER; PINHEAD_3X1
U$3: HW-RSC; HONEYWELL-8

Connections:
3.3V: SPI2.1, U$3.6 (VCC)
CS: U$1.3 (5), U$3.7 (CS_EE)
CS2: SPI2.3
CS3: SPI2.2
EOC/CS1: U$1.1, U$3.4 (CS_ADC)
GND: SPI2.7, U$1.2 (3), U$3.5 (GND)
MISO: SPI2.5, U$3.8 (DOUT)
MOSI: SPI2.4, U$3.3 (DIN)
SCK: SPI2.6, U$3.1 (SCLK)

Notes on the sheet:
8. Dez. 2018
(c) www.olliw.eu
UC4H Airspeed Node RSC ADDON
Schaltplan v0.4.0
This is a open source hardware project, under the terms of the TAPR Open Hardware License, http://www.tapr.org/ohl.html. The project web page is http://www.olliw.eu/.
1/1

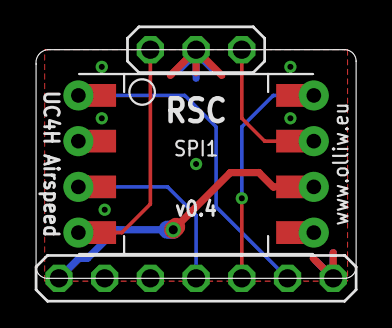
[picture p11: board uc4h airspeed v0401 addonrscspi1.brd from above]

Board: 2 copper layers, 17.8 x 12.7 mm, 3 parts (0 on the bottom side), 7 nets.

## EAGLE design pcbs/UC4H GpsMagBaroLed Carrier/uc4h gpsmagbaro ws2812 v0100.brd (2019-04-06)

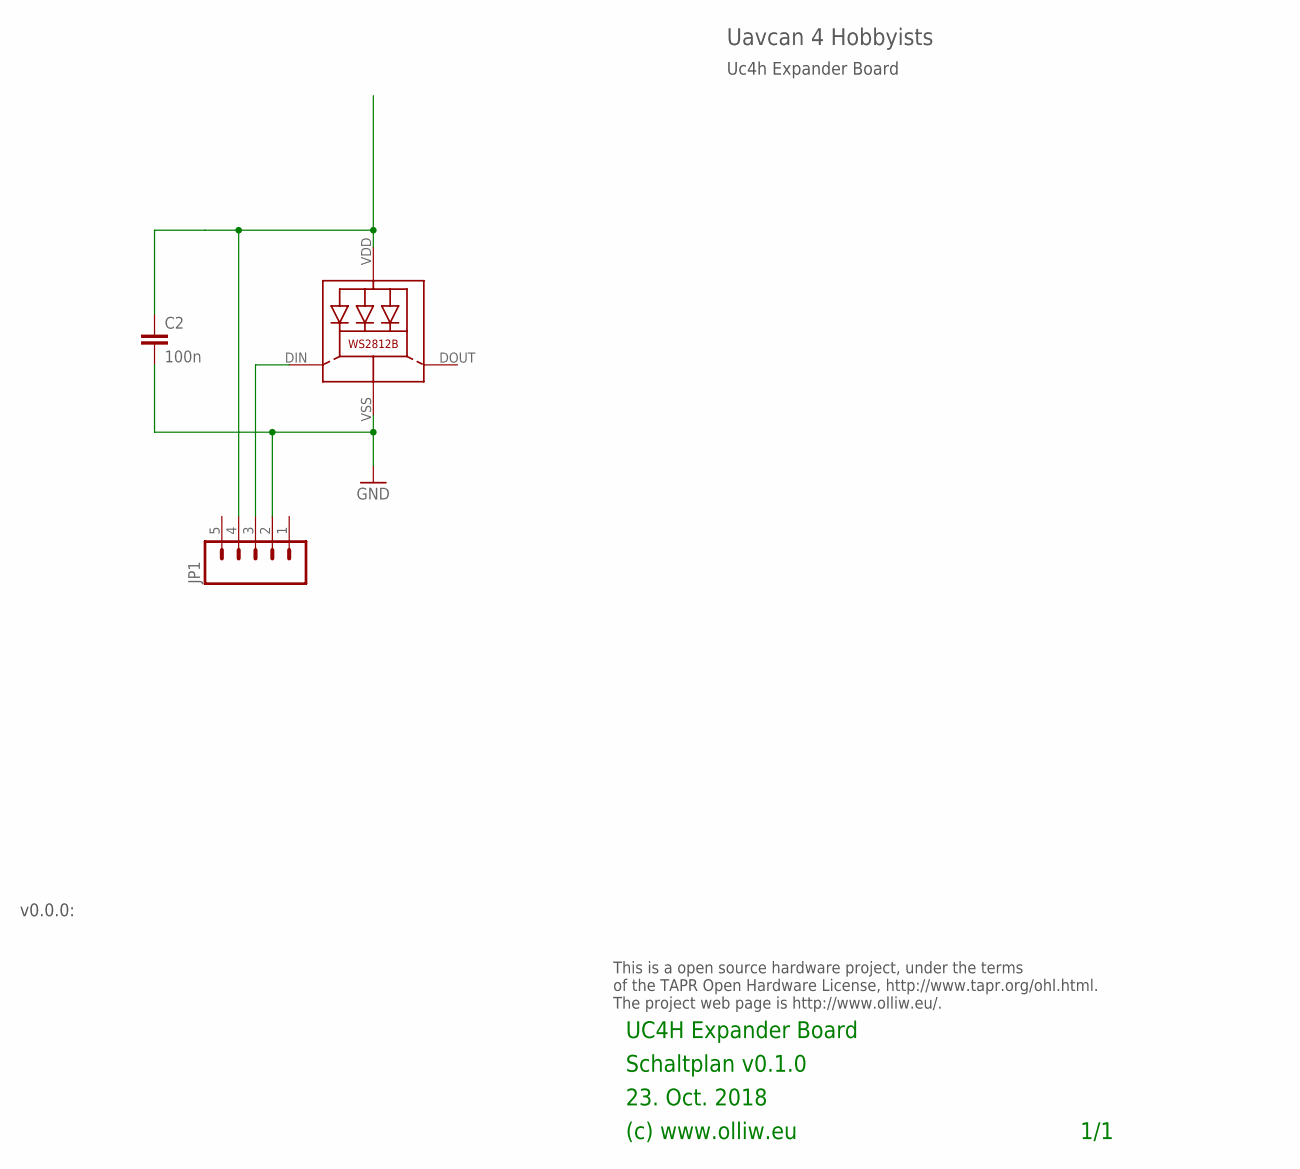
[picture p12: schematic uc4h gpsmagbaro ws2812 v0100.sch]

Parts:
C2: 100n; C0402
JP1: M05PTH; 1X05
LED1: WS2812B

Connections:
GND: C2.2, JP1.2, LED1.VSS (GND)
unnamed: JP1.3, LED1.DIN (DI)
unnamed: C2.1, JP1.4, LED1.VDD

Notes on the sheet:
23. Oct. 2018
(c) www.olliw.eu
UC4H Expander Board
Schaltplan v0.1.0
This is a open source hardware project, under the terms of the TAPR Open Hardware License, http://www.tapr.org/ohl.html. The project web page is http://www.olliw.eu/.
1/1
Uc4h Expander Board
Uavcan 4 Hobbyists
v0.0.0:

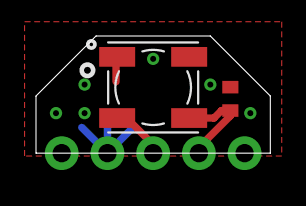
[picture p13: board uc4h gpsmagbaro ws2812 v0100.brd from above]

Board: 2 copper layers, 13.0 x 6.5 mm, 3 parts (0 on the bottom side), 3 nets.

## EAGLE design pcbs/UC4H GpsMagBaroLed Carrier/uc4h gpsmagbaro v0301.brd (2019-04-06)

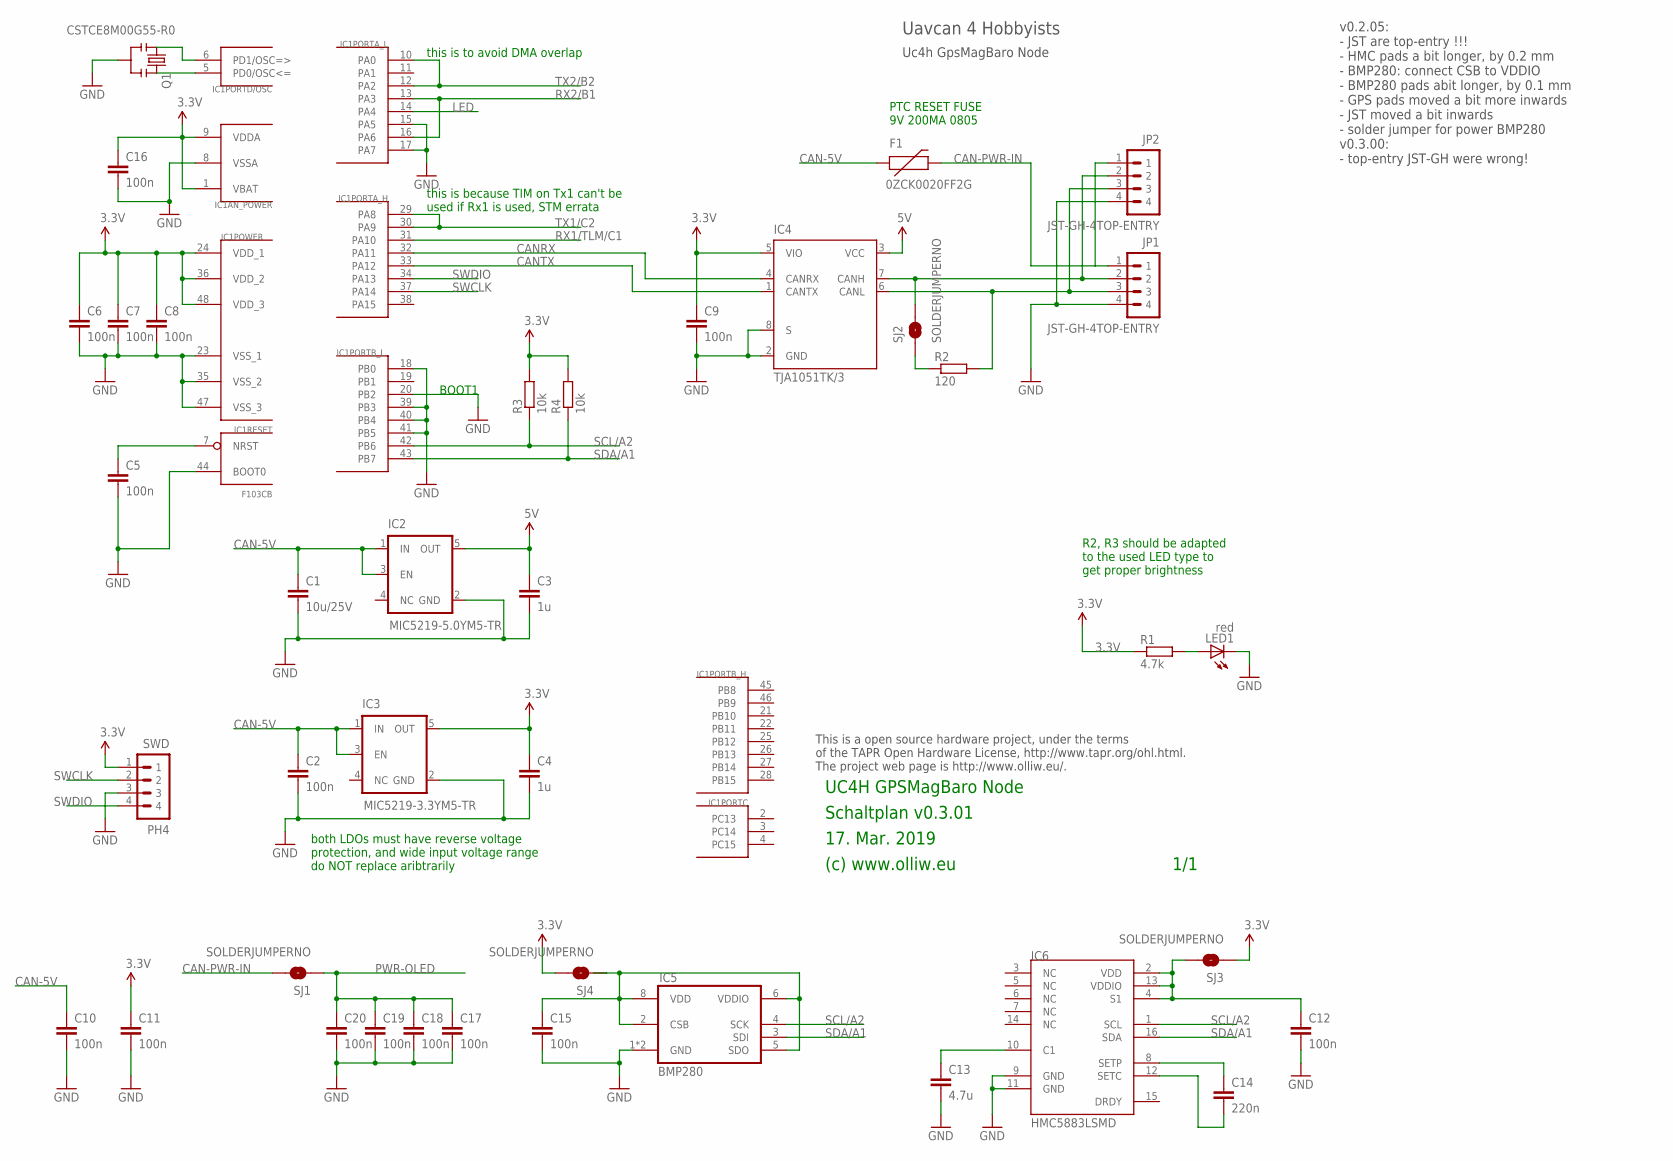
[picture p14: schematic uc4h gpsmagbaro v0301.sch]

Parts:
C1: 10u/25V; C1206
C2, C5, C6, C7, C8, C9: 100n; C0603K
C3, C4: 1u; C0603K
C10, C11, C12, C15, C16, C17, C18, C19, C20: 100n; C0603
C13: 4.7u; C0805
C14: 220n; C0603
F1: 0ZCK0020FF2G; FUSE-0805
IC1: F103CB; TQFP48
IC2: MIC5219-5.0YM5-TR; SOT23-5
IC3: MIC5219-3.3YM5-TR; SOT23-5
IC4: TJA1051TK/3; HVSON8
IC5: BMP280
IC6: HMC5883LSMD; 16LPCC
JP1, JP2: JST-GH-4TOP-ENTRY; BM04B-GHS-TBT
LED1: red; CHIPLED_0603
Q1: CSTCE8M00G55-R0; RESONATOR-SMD
R1: 4.7k; R0603
R2: 120; R0603
R3, R4: 10k; R0603
SJ1, SJ2, SJ3, SJ4: SOLDERJUMPERNO; SJ_2S-NO
SWD: PH4; 4X1_1P27_OCT_BILEX

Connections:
3.3V: C4.1, C6.1, C7.1, C8.1, C9.1, C11.1, C16.1, IC1.1 (VBAT), IC1.9 (VDDA), IC1.24 (VDD_1), IC1.36 (VDD_2), IC1.48 (VDD_3), IC3.5 (OUT), IC4.5 (VIO), R1.1, R3.2, R4.2, SJ3.1, SJ4.2, SWD.1
5V: C3.1, IC2.5 (OUT), IC4.3 (VCC)
CAN-5V: C1.1, C2.1, C10.1, F1.1, IC2.1 (IN), IC2.3 (EN), IC3.1 (IN), IC3.3 (EN)
CAN-PWR-IN: F1.2, JP1.1, JP2.1, SJ1.2
CANH: IC4.7 (CANH), JP1.2, JP2.2, SJ2.2
CANL: IC4.6 (CANL), JP1.3, JP2.3, R2.2
CANRX: IC1.32 (PA11), IC4.4 (CANRX)
CANTX: IC1.33 (PA12), IC4.1 (CANTX)
GND: C1.2, C2.2, C3.2, C4.2, C5.2, C6.2, C7.2, C8.2, C9.2, C10.2, C11.2, C12.2, C13.2, C15.2, C16.2, C17.2, C18.2, C19.2, C20.2, IC1.8 (VSSA), IC1.15 (PA5), IC1.17 (PA7), IC1.18 (PB0), IC1.20 (PB2), IC1.23 (VSS_1), IC1.35 (VSS_2), IC1.39 (PB3), IC1.40 (PB4), IC1.41 (PB5), IC1.44 (BOOT0), IC1.47 (VSS_3), IC2.2 (GND), IC3.2 (GND), IC4.2 (GND), IC4.8 (S), IC5.1 (GND), IC5.7 (GND), IC6.9 (GND), IC6.11 (GND), JP1.4, JP2.4, LED1.C, Q1.2, SWD.3
LED: IC1.14 (PA4)
unnamed: C5.1, IC1.7 (NRST)
unnamed: C12.1, IC6.2 (VDD), IC6.4 (S1), IC6.13 (VDDIO), SJ3.2
unnamed: R2.1, SJ2.1
unnamed: IC1.6 (PD1/OSC=>), Q1.1
unnamed: IC1.5 (PD0/OSC<=), Q1.3
unnamed: C14.1, IC6.8 (SETP)
unnamed: C15.1, IC5.2 (CSB), IC5.5 (SDO), IC5.6 (VDDIO), IC5.8 (VDD), SJ4.1
unnamed: LED1.A, R1.2
unnamed: C14.2, IC6.12 (SETC)
unnamed: C13.1, IC6.10 (C1)
PWR-OLED: C17.1, C18.1, C19.1, C20.1, SJ1.1
RX1/TLM/C1: IC1.31 (PA10)
RX2/B1: IC1.13 (PA3), IC1.16 (PA6)
SCL/A2: IC1.42 (PB6), IC5.4 (SCK), IC6.1 (SCL), R3.1
SDA/A1: IC1.43 (PB7), IC5.3 (SDI), IC6.16 (SDA), R4.1
SWCLK: IC1.37 (PA14), SWD.2
SWDIO: IC1.34 (PA13), SWD.4
TX1/C2: IC1.29 (PA8), IC1.30 (PA9)
TX2/B2: IC1.10 (PA0), IC1.12 (PA2)

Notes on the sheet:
17. Mar. 2019
(c) www.olliw.eu
UC4H GPSMagBaro Node
Schaltplan v0.3.01
This is a open source hardware project, under the terms of the TAPR Open Hardware License, http://www.tapr.org/ohl.html. The project web page is http://www.olliw.eu/.
1/1
Uc4h GpsMagBaro Node
Uavcan 4 Hobbyists
BOOT1
PTC RESET FUSE 9V 200MA 0805
both LDOs must have reverse voltage protection, and wide input voltage range do NOT replace aribtrarily
this is to avoid DMA overlap
this is because TIM on Tx1 can't be used if Rx1 is used, STM errata
v0.2.05: - JST are top-entry !!! - HMC pads a bit longer, by 0.2 mm - BMP280: connect CSB to VDDIO - BMP280 pads abit longer, by 0.1 mm - GPS pads moved a bit more inwards - JST moved a bit inwards - solder jumper for power BMP280 v0.3.00: - top-entry JST-GH were wrong!
R2, R3 should be adapted to the used LED type to get proper brightness

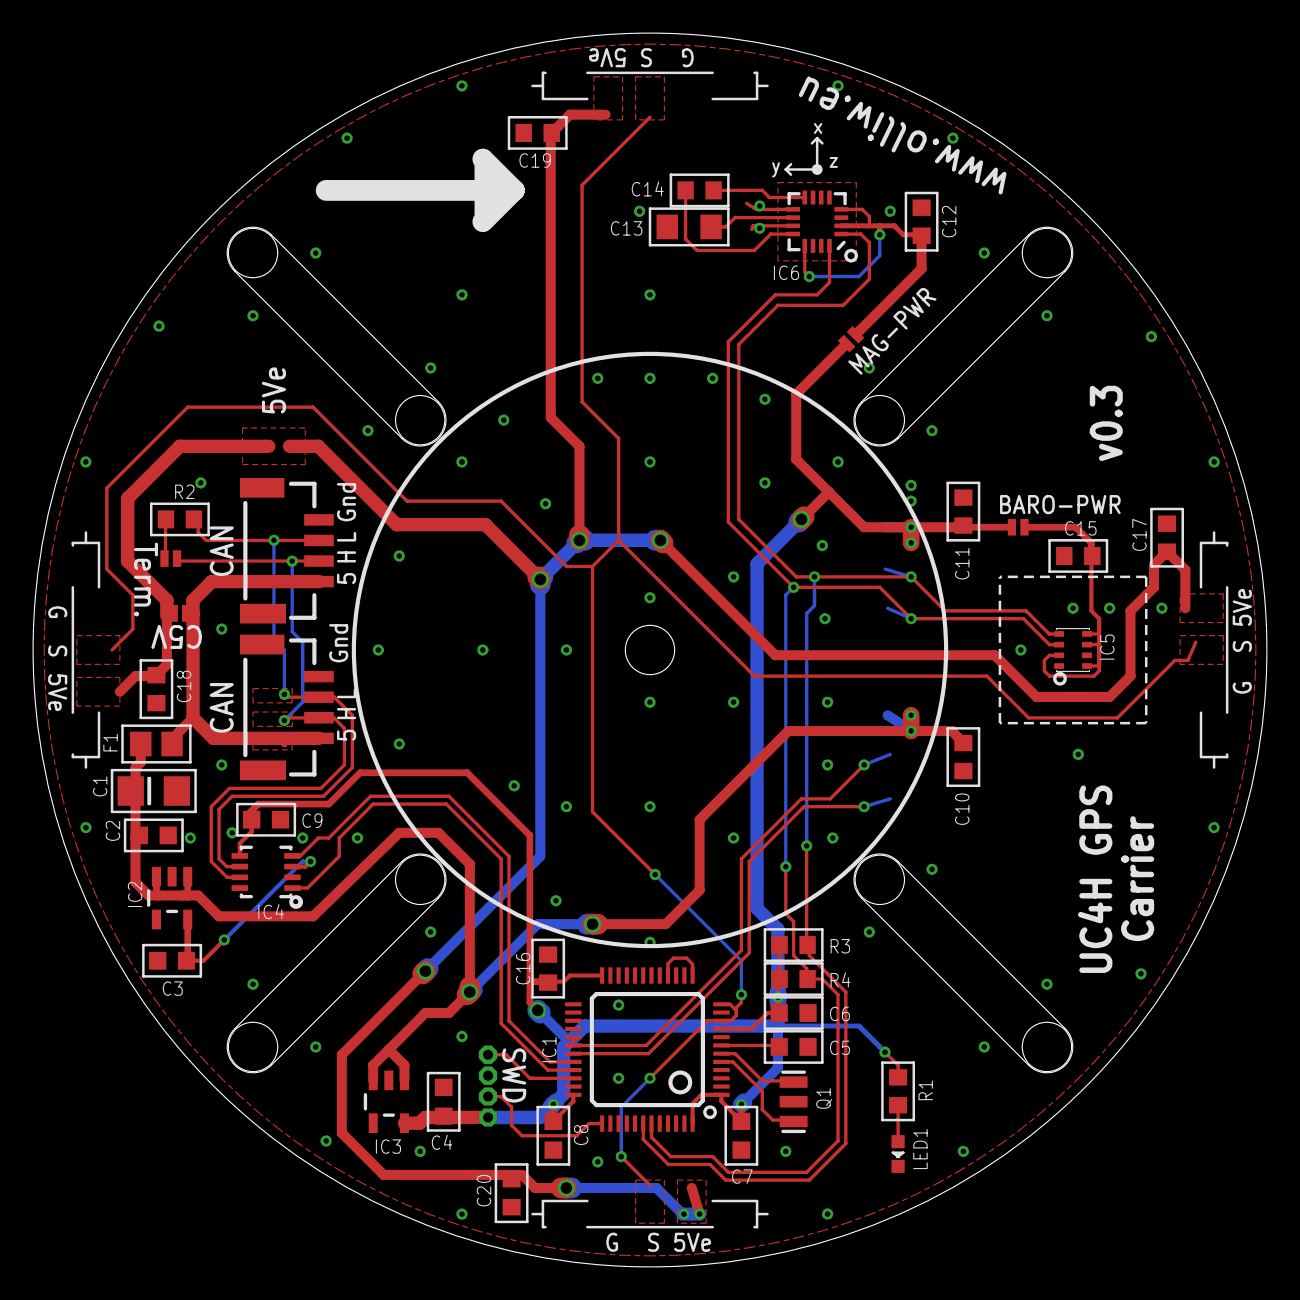
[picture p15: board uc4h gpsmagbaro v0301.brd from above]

Board: 2 copper layers, 75.0 x 75.0 mm, 40 parts (0 on the bottom side), 27 nets.

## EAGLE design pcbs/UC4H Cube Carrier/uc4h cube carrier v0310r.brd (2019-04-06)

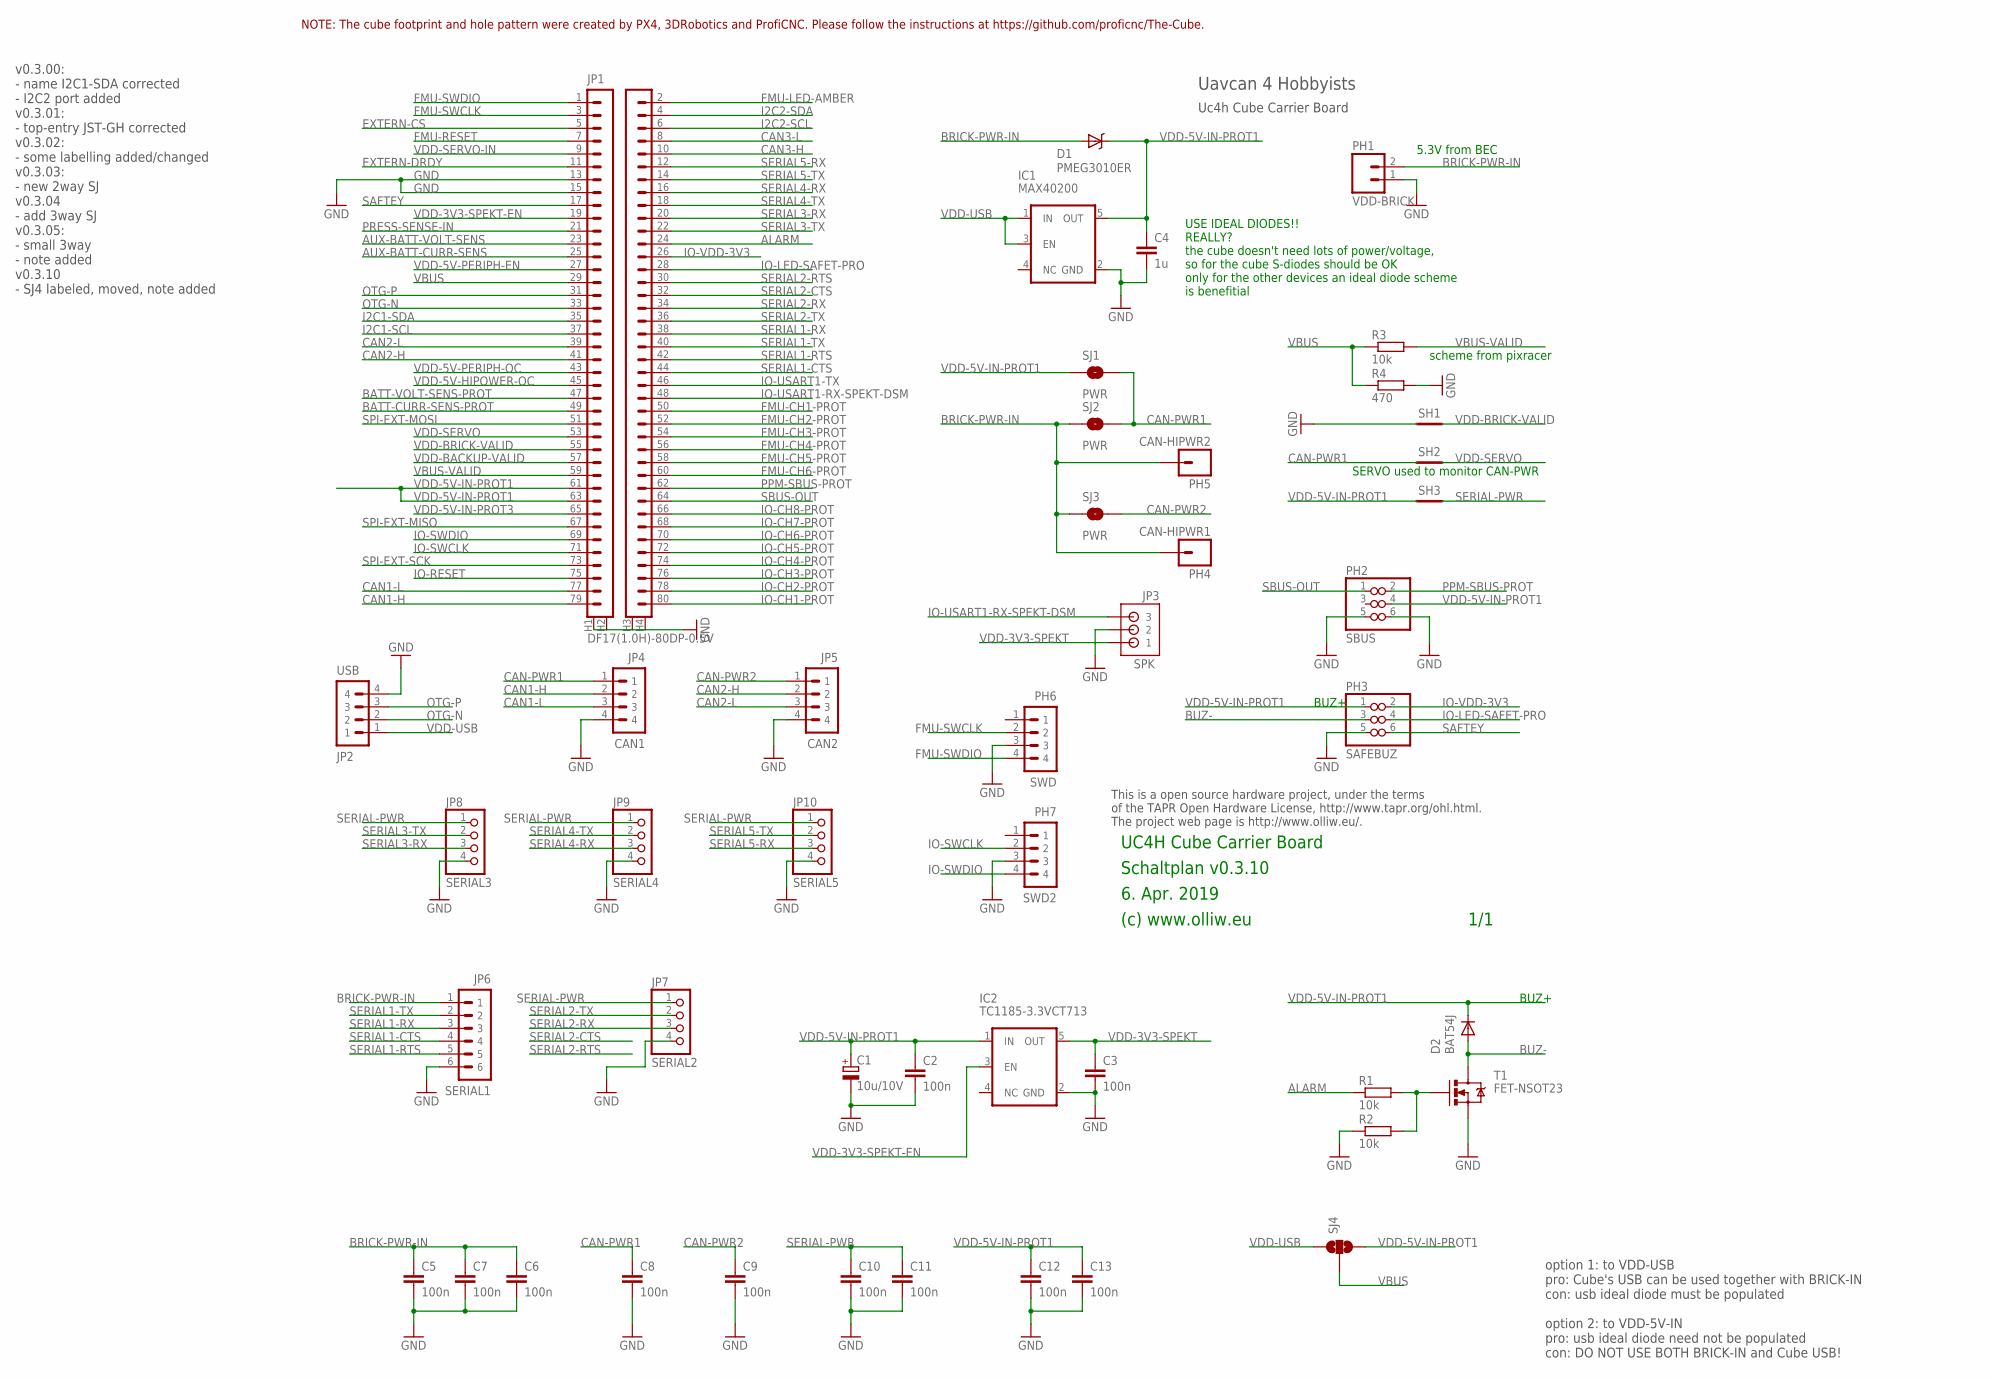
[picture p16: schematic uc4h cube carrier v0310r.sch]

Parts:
C1: 10u/10V; SMC_A
C2, C3, C5, C6, C8, C9, C10, C11, C12, C13: 100n; C0603
C4: 1u; C0603
C7: 100n; C0402
D1: PMEG3010ER; SOD123W-DIODE
D2: BAT54J; SOD110-R
IC1: MAX40200; SOT23-5
IC2: TC1185-3.3VCT713; SOT23-5
JP1: DF17(1.0H)-80DP-0.5V; PIX-CUBE-DF17(1.0H)-80DP-0.5V-VIA
JP2: USB; BM04B-GHS-TBT
JP3: SPK; B3B-ZR
JP4: CAN1; BM04B-GHS-TBT
JP5: CAN2; BM04B-GHS-TBT
JP6: SERIAL1; BM06B-GHS-TBT
JP7: SERIAL2; PINHEAD_4X1
JP8: SERIAL3; PINHEAD_4X1
JP9: SERIAL4; PINHEAD_4X1
JP10: SERIAL5; PINHEAD_4X1
PH1: VDD-BRICK; 1X02
PH2: SBUS; PINHEAD_3X2
PH3: SAFEBUZ; PINHEAD_3X2
PH4: CAN-HIPWR1; 1X01
PH5: CAN-HIPWR2; 1X01
PH6: SWD; 4X1_1P27_OCT_BILEX
PH7: SWD2; 4X1_1P27_OCT_BILEX
R1, R2, R3: 10k; R0402
R4: 470; R0402
SH1, SH2, SH3: SHORT-HT5; SHORT_TOP-50
SJ1, SJ3: PWR; SJ-2WAY-BIG-WPASTEC
SJ2: PWR; SJ-2WAY-BIG
SJ4: SJ-3WAY-03; SJ-3WAY-WPASTEC
T1: FET-NSOT23; SOT23

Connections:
ALARM: JP1.24, R1.1
AUX-BATT-CURR-SENS: JP1.25
AUX-BATT-VOLT-SENS: JP1.23
BATT-CURR-SENS-PROT: JP1.49
BATT-VOLT-SENS-PROT: JP1.47
BRICK-PWR-IN: C5.1, C6.1, C7.1, D1.A, JP6.1, PH1.2, PH4.1, PH5.1, SJ2.1, SJ3.1
BUZ-: D2.A, PH3.3, T1.3 (D)
CAN1-H: JP1.79, JP4.2
CAN1-L: JP1.77, JP4.3
CAN2-H: JP1.41, JP5.2
CAN2-L: JP1.39, JP5.3
CAN3-H: JP1.10
CAN3-L: JP1.8
CAN-PWR1: C8.1, JP4.1, SH2.1, SJ1.2, SJ2.2
CAN-PWR2: C9.1, JP5.1, SJ3.2
EXTERN-CS: JP1.5
EXTERN-DRDY: JP1.11
FMU-CH1-PROT: JP1.50
FMU-CH2-PROT: JP1.52
FMU-CH3-PROT: JP1.54
FMU-CH4-PROT: JP1.56
FMU-CH5-PROT: JP1.58
FMU-CH6-PROT: JP1.60
FMU-LED-AMBER: JP1.2
FMU-RESET: JP1.7
FMU-SWCLK: JP1.3, PH6.2
FMU-SWDIO: JP1.1, PH6.4
GND: C1.-, C2.2, C3.2, C4.2, C5.2, C6.2, C7.2, C8.2, C9.2, C10.2, C11.2, C12.2, C13.2, IC1.2 (GND), IC2.2 (GND), JP1.13, JP1.15, JP1.H1 (81), JP1.H2 (82), JP1.H3 (83), JP1.H4 (84), JP2.4, JP3.2, JP4.4, JP5.4, JP6.6, JP7.4, JP8.4, JP9.4, JP10.4, PH1.1, PH2.5, PH2.6, PH3.5, PH6.3, PH7.3, R2.1, R4.2, SH1.1, T1.2 (S)
I2C1-SCL: JP1.37
I2C1-SDA: JP1.35
I2C2-SCL: JP1.6
I2C2-SDA: JP1.4
IO-CH1-PROT: JP1.80
IO-CH2-PROT: JP1.78
IO-CH3-PROT: JP1.76
IO-CH4-PROT: JP1.74
IO-CH5-PROT: JP1.72
IO-CH6-PROT: JP1.70
IO-CH7-PROT: JP1.68
IO-CH8-PROT: JP1.66
IO-LED-SAFET-PRO: JP1.28, PH3.4
IO-RESET: JP1.75
IO-SWCLK: JP1.71, PH7.2
IO-SWDIO: JP1.69, PH7.4
IO-USART1-RX-SPEKT-DSM: JP1.48, JP3.3
IO-USART1-TX: JP1.46
IO-VDD-3V3: JP1.26, PH3.2
unnamed: R1.2, R2.2, T1.1 (G)
OTG-N: JP1.33, JP2.2
OTG-P: JP1.31, JP2.3
PPM-SBUS-PROT: JP1.62, PH2.2
PRESS-SENSE-IN: JP1.21
SAFTEY: JP1.17, PH3.6
SBUS-OUT: JP1.64, PH2.1
SERIAL1-CTS: JP1.44, JP6.4
SERIAL1-RTS: JP1.42, JP6.5
SERIAL1-RX: JP1.38, JP6.3
SERIAL1-TX: JP1.40, JP6.2
SERIAL2-CTS: JP1.32
SERIAL2-RTS: JP1.30
SERIAL2-RX: JP1.34, JP7.3
SERIAL2-TX: JP1.36, JP7.2
SERIAL3-RX: JP1.20, JP8.3
SERIAL3-TX: JP1.22, JP8.2
SERIAL4-RX: JP1.16, JP9.3
SERIAL4-TX: JP1.18, JP9.2
SERIAL5-RX: JP1.12, JP10.3
SERIAL5-TX: JP1.14, JP10.2
SERIAL-PWR: C10.1, C11.1, JP7.1, JP8.1, JP9.1, JP10.1, SH3.2
SPI-EXT-MISO: JP1.67
SPI-EXT-MOSI: JP1.51
SPI-EXT-SCK: JP1.73
VBUS: JP1.29, R3.1, R4.1, SJ4.2
VBUS-VALID: JP1.59, R3.2
VDD-3V3-SPEKT: C3.1, IC2.5 (OUT), JP3.1
VDD-3V3-SPEKT-EN: IC2.3 (EN), JP1.19
VDD-5V-HIPOWER-OC: JP1.45
VDD-5V-IN-PROT1: C1.+, C2.1, C4.1, C12.1, C13.1, D1.C, D2.C, IC1.5 (OUT), IC2.1 (IN), JP1.61, JP1.63, PH2.4, PH3.1, SH3.1, SJ1.1, SJ4.3
VDD-5V-IN-PROT3: JP1.65
VDD-5V-PERIPH-EN: JP1.27
VDD-5V-PERIPH-OC: JP1.43
VDD-BACKUP-VALID: JP1.57
VDD-BRICK-VALID: JP1.55, SH1.2
VDD-SERVO: JP1.53, SH2.2
VDD-SERVO-IN: JP1.9
VDD-USB: IC1.1 (IN), IC1.3 (EN), JP2.1, SJ4.1

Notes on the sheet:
6. Apr. 2019
(c) www.olliw.eu
UC4H Cube Carrier Board
Schaltplan v0.3.10
This is a open source hardware project, under the terms of the TAPR Open Hardware License, http://www.tapr.org/ohl.html. The project web page is http://www.olliw.eu/.
1/1
Uc4h Cube Carrier Board
Uavcan 4 Hobbyists
v0.3.00: - name I2C1-SDA corrected - I2C2 port added v0.3.01: - top-entry JST-GH corrected v0.3.02: - some labelling added/changed v0.3.03: - new 2way SJ v0.3.04 - add 3way SJ v0.3.05: - small 3way - note added v0.3.10 - SJ4 labeled, moved, note added
5.3V from BEC
USE IDEAL DIODES!! REALLY? the cube doesn't need lots of power/voltage, so for the cube S-diodes should be OK only for the other devices an ideal diode scheme is benefitial
SERVO used to monitor CAN-PWR
scheme from pixracer
BUZ+
NOTE: The cube footprint and hole pattern were created by PX4, 3DRobotics and ProfiCNC. Please follow the instructions at https://github.com/proficnc/The-Cube.
option 1: to VDD-USB pro: Cube's USB can be used together with BRICK-IN con: usb ideal diode must be populated option 2: to VDD-5V-IN pro: usb ideal diode need not be populated con: DO NOT USE BOTH BRICK-IN and Cube USB!

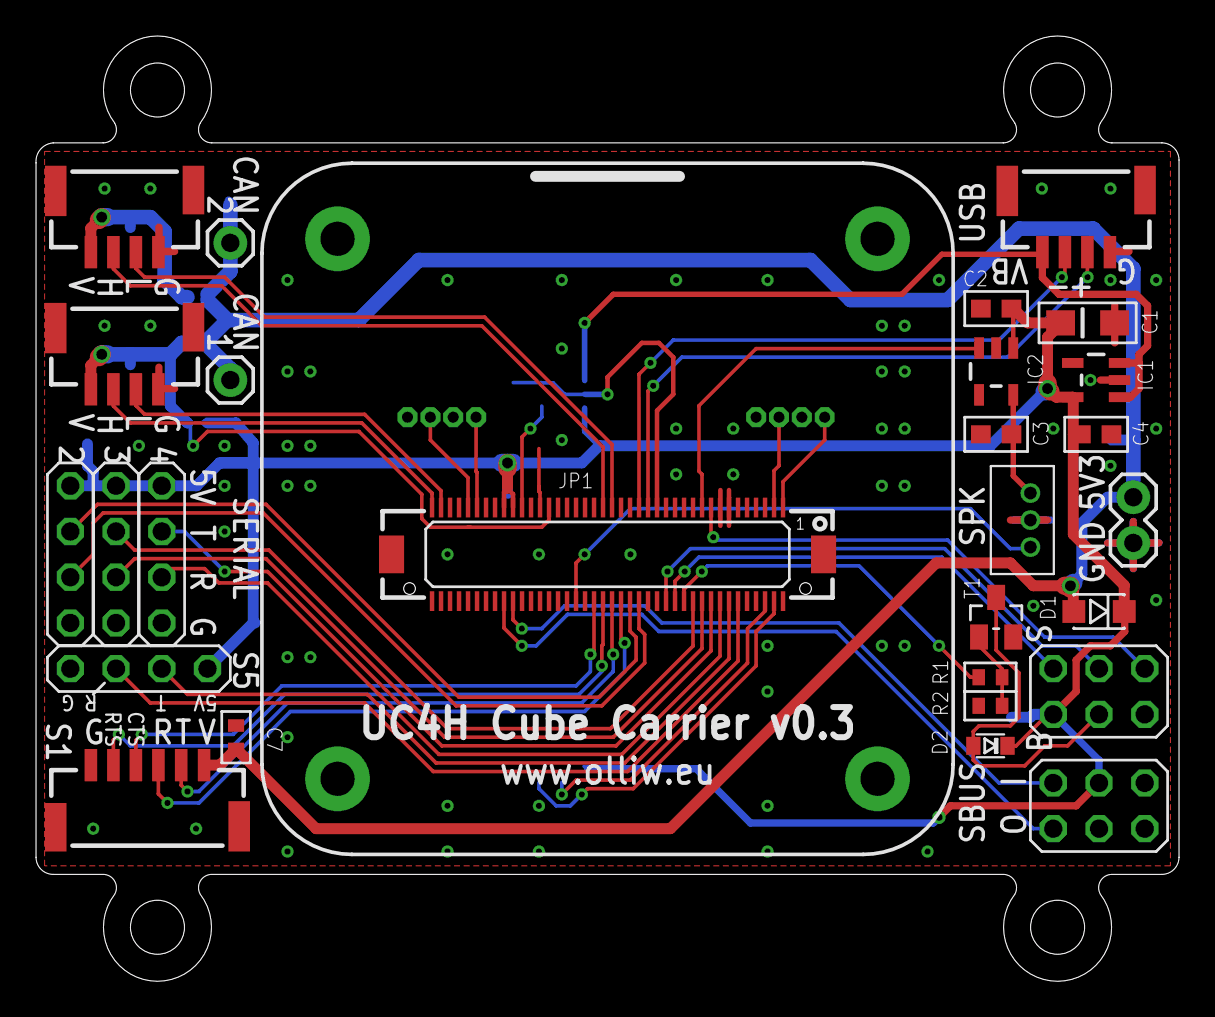
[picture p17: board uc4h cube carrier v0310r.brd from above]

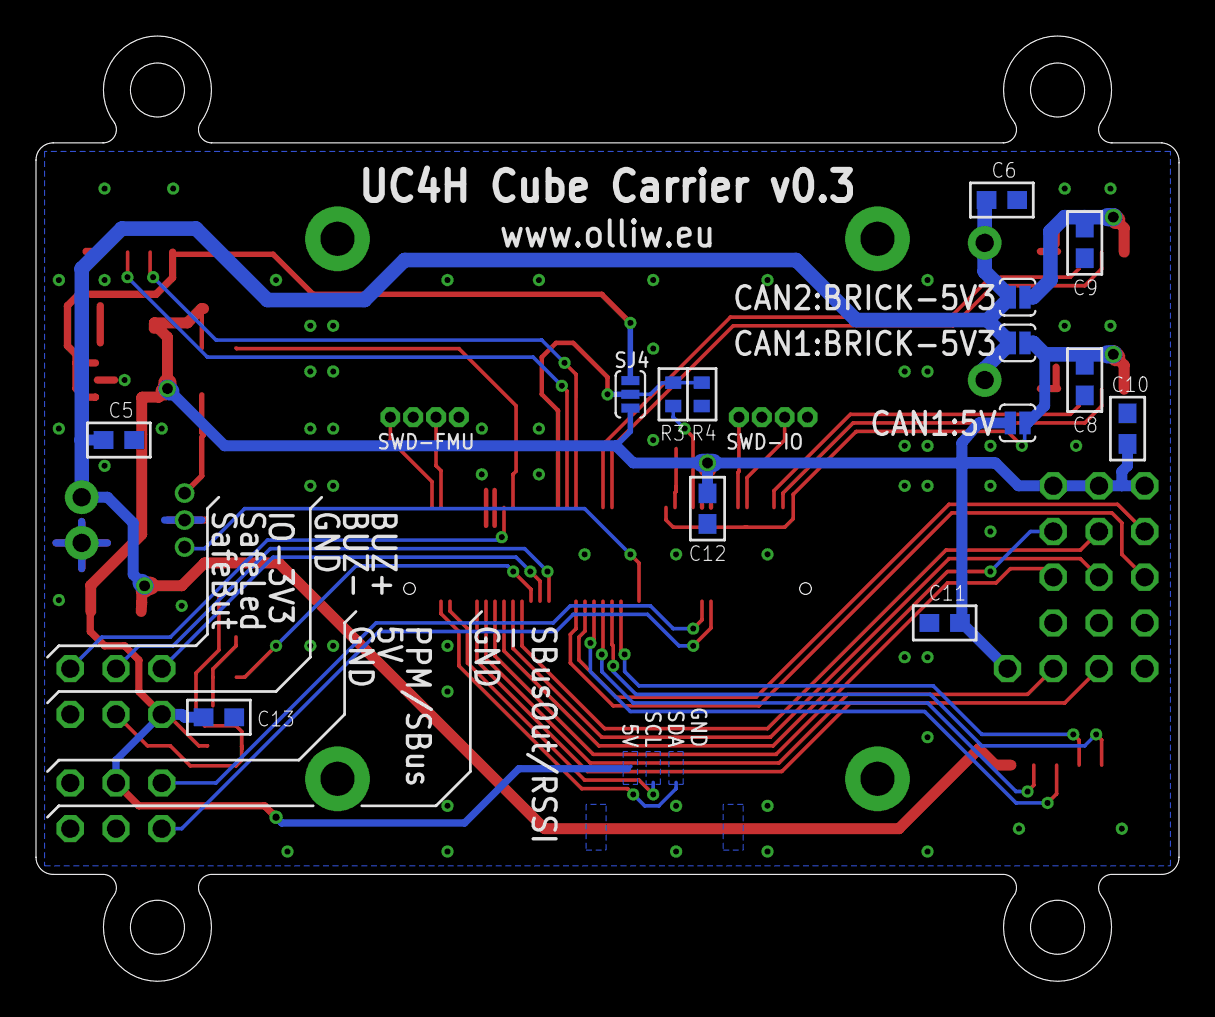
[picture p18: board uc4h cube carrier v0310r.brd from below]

Board: 2 copper layers, 63.5 x 52.5 mm, 46 parts (15 on the bottom side), 44 nets.

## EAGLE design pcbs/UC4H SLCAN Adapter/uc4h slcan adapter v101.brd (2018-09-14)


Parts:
5V-EXT: PH2; 1X02
C1: 10u/10V; C1206
C2, C4, C5, C6, C7, C8, C9, C11: 100n; C0603K
C3: 1u; C0603K
C10: 4.7u; C0805
CAN#1, CAN#2: JST-GH-4; SM04B-GHS-TB
CAN#3, CAN#4: PH4; 1X04
CAN-5V-SRC: PH2; 1X02
CAN-PWR: PH2; 1X02
D1, D2, D3: PMEG3010ER; SOD123W-DIODE
F1: FUSE-PTC; FUSE-1206
IC1: STM32F103T8; VFQFPN36
IC2: MIC5219-3.3YM5-TR; SOT23-5
IC3: TJA1051TK/3; HVSON8
IC4: CP2102N-QFN24; QFN24-CP2102N
JP4: PH2; 1X02
LED1: red; CHIPLED_0603
LED2, LED4: green; CHIPLED_0603
LED3, LED5: yellow; CHIPLED_0603
Q1: CSTCE8M00G55-R0; RESONATOR-SMD
R1: 10k; R0603
R2: 4.7k; R0603
R3, R4, R6, R7: 2.2k; R0603
R5: 1k; R0603
SJ1: BOOT0; SJ_2S-NO
SWD: PH4; 4X1_1P27_OCT_BILEX
UART2: PH4; 1X04
USB: Amphenol 10118192-0001LF; USB-MICROB

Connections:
3.3V: C3.1, C5.1, C6.1, C7.1, C8.1, IC1.1 (VDD_3), IC1.6 (VDDA), IC1.19 (VDD_1), IC1.27 (VDD_2), IC2.5 (OUT), IC3.5 (VIO), R2.1, SJ1.1, SWD.1, UART2.1
3.3V-CP2102: C11.1, IC4.5 (VIO), IC4.6 (3.3VOUT), R5.2, R6.2, R7.2
5V: C1.1, C2.1, CAN-5V-SRC.1, D1.C, D2.C, D3.C, IC2.1 (IN), IC2.3 (EN)
5V-CAN-FUSE: D1.A, F1.4 (2)
CAN-PWR: CAN#1.1, CAN#2.1, CAN#3.1, CAN#4.1, CAN-5V-SRC.2, CAN-PWR.2, F1.3 (1), IC3.3 (VCC)
CANH: CAN#1.2, CAN#2.2, CAN#3.2, CAN#4.2, IC3.7 (CANH), JP4.2
CANL: CAN#1.3, CAN#2.3, CAN#3.3, CAN#4.3, IC3.6 (CANL), JP4.1
CANRX: IC1.23 (PA11), IC3.4 (CANRX)
CANTX: IC1.24 (PA12), IC3.1 (CANTX)
GND: 5V-EXT.1, C1.2, C2.2, C3.2, C4.2, C5.2, C6.2, C7.2, C8.2, C9.2, C10.2, C11.2, CAN#1.4, CAN#2.4, CAN#3.4, CAN#4.4, CAN-PWR.1, IC1.5 (VSSA), IC1.17 (PB2), IC1.18 (VSS_1), IC1.26 (VSS_2), IC1.36 (VSS_3), IC2.2 (GND), IC3.2 (GND), IC3.8 (S), IC4.2 (GND), LED1.C, LED2.C, LED3.C, Q1.2, R1.1, SWD.3, UART2.4, USB.GND
LED: IC1.11 (PA4), R4.1
LEDB: IC1.12 (PA5), R3.1
unnamed: C4.1, IC1.4 (NRST)
unnamed: LED3.A, R3.2
unnamed: IC1.35 (BOOT0), R1.2, SJ1.2
unnamed: IC1.2 (PD0/OSC<=), Q1.1
unnamed: IC1.3 (PD1/OSC=>), Q1.3
unnamed: LED2.A, R4.2
unnamed: LED1.A, R2.2
unnamed: 5V-EXT.2, D3.A
unnamed: IC4.9 (RST), R5.1
unnamed: LED4.A, R6.1
unnamed: IC4.4 (D-), USB.D-
unnamed: LED5.A, R7.1
unnamed: IC4.3 (D+), USB.D+
RX1: IC1.22 (PA10), IC4.21 (TXD), LED5.C
RX2: IC1.10 (PA3), UART2.3
SWCLK: IC1.28 (PA14), SWD.2
SWDIO: IC1.25 (PA13), SWD.4
TX1: IC1.21 (PA9), IC4.20 (RXD), LED4.C
TX2: IC1.9 (PA2), UART2.2
VUSB: C9.1, C10.1, D2.A, IC4.7 (VREGIN), IC4.8 (VBUS), USB.VBUS

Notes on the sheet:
14. Sep. 2018
(c) www.olliw.eu
UC4H SLCAN Adapter
Schaltplan v1.01
This is a open source hardware project, under the terms of the TAPR Open Hardware License, http://www.tapr.org/ohl.html. The project web page is http://www.olliw.eu/.
1/1
Uc4h SLCAN Adapter
Uavcan 4 Hobbiests
BOOT1
v1.01: - 3.3 LDO - frames
PTC RESET FUSE


Board: 2 copper layers, 29.8 x 34.9 mm, 44 parts (0 on the bottom side), 32 nets.

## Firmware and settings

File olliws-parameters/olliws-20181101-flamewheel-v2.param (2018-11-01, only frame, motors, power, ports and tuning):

ATC_ANG_LIM_TC,1
ATC_ANG_PIT_P,12
ATC_ANG_RLL_P,12
ATC_ANG_YAW_P,6
ATC_ANGLE_BOOST,1
ATC_RAT_PIT_D,0.008
ATC_RAT_PIT_FF,0
ATC_RAT_PIT_FILT,20
ATC_RAT_PIT_I,0.12136
ATC_RAT_PIT_IMAX,0.5
ATC_RAT_PIT_P,0.12136
ATC_RAT_RLL_D,0.008
ATC_RAT_RLL_FF,0
ATC_RAT_RLL_FILT,20
ATC_RAT_RLL_I,0.12136
ATC_RAT_RLL_IMAX,0.5
ATC_RAT_RLL_P,0.12136
ATC_RAT_YAW_D,0
ATC_RAT_YAW_FF,0
ATC_RAT_YAW_FILT,1.617667
ATC_RAT_YAW_I,0.1087801
ATC_RAT_YAW_IMAX,0.5
ATC_RAT_YAW_P,1.087801
ATC_RATE_FF_ENAB,1
ATC_RATE_P_MAX,0
ATC_RATE_R_MAX,0
ATC_RATE_Y_MAX,0
BATT_AMP_OFFSET,0
BATT_AMP_PERVLT,22
BATT_CAPACITY,5200
BATT_CRT_MAH,0
BATT_CRT_VOLT,0
BATT_CURR_PIN,-1
BATT_FS_CRT_ACT,0
BATT_FS_LOW_ACT,0
BATT_FS_VOLTSRC,0
BATT_LOW_MAH,0
BATT_LOW_TIMER,10
BATT_LOW_VOLT,10.5
BATT_MONITOR,83
BATT_SERIAL_NUM,1
BATT_VOLT_MULT,10
BATT_VOLT_PIN,-1
BATT2_MONITOR,0
FLTMODE_CH,5
FLTMODE1,0
FLTMODE2,0
FLTMODE3,0
FLTMODE4,2
FLTMODE5,0
FLTMODE6,16
FRAME_CLASS,1
FRAME_TYPE,1
INS_GYRO_FILTER,20
MOT_BAT_CURR_MAX,0
MOT_BAT_CURR_TC,5
MOT_BAT_IDX,0
MOT_BAT_VOLT_MAX,0
MOT_BAT_VOLT_MIN,0
MOT_BOOST_SCALE,0
MOT_HOVER_LEARN,2
MOT_PWM_MAX,2000
MOT_PWM_MIN,1000
MOT_PWM_TYPE,0
MOT_SAFE_DISARM,0
MOT_SPIN_ARM,0.1
MOT_SPIN_MAX,0.95
MOT_SPIN_MIN,0.15
MOT_SPOOL_TIME,0.5
MOT_THST_EXPO,0.65
MOT_THST_HOVER,0.4767646
MOT_YAW_HEADROOM,200
SERIAL0_BAUD,115
SERIAL0_PROTOCOL,2
SERIAL1_BAUD,57
SERIAL1_PROTOCOL,1
SERIAL2_BAUD,115
SERIAL2_PROTOCOL,-1
SERIAL3_BAUD,38
SERIAL3_PROTOCOL,5
SERIAL4_BAUD,38
SERIAL4_PROTOCOL,1
SERIAL5_BAUD,57
SERIAL5_PROTOCOL,-1
SERIAL6_BAUD,57
SERIAL6_PROTOCOL,-1
SERVO1_FUNCTION,33
SERVO1_MAX,1920
SERVO1_MIN,1080
SERVO1_REVERSED,0
SERVO1_TRIM,1500
SERVO2_FUNCTION,34
SERVO2_MAX,1920
SERVO2_MIN,1080
SERVO2_REVERSED,0
SERVO2_TRIM,1500
SERVO3_FUNCTION,35
SERVO3_MAX,1920
SERVO3_MIN,1080
SERVO3_REVERSED,0
SERVO3_TRIM,1500
SERVO4_FUNCTION,36
SERVO4_MAX,1920
SERVO4_MIN,1080
SERVO4_REVERSED,0
SERVO4_TRIM,1500
SERVO5_FUNCTION,0
SERVO5_MAX,1822
SERVO5_MIN,1076
SERVO5_REVERSED,0
SERVO5_TRIM,1076
SERVO6_FUNCTION,16
SERVO6_MAX,1496
SERVO6_MIN,1078
SERVO6_REVERSED,0
SERVO6_TRIM,1496
SERVO7_FUNCTION,0
SERVO7_MAX,1900
SERVO7_MIN,1100
SERVO7_REVERSED,0
SERVO7_TRIM,898
SERVO8_FUNCTION,0
SERVO8_MAX,1900
SERVO8_MIN,1100
SERVO8_REVERSED,0
SERVO8_TRIM,0
SERVO9_FUNCTION,0
SERVO9_MAX,1900
SERVO9_MIN,1100
SERVO9_REVERSED,0
SERVO9_TRIM,1500

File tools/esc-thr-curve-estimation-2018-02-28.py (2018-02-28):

#!/usr/bin/env python3
'''
measurement of rpm vs pwm and I vs pwm, using a UC4H ESC KISS32A node
=> calculation of estimated thrust vs pwm
=> fit to poly function to estimate MOT_THST_EXPO parameter

OlliW 28.Feb.2018
'''

#based on the example here: http://uavcan.org/Implementations/Pyuavcan/Examples/ESC_throttle_control/
#see https://groups.google.com/forum/#!topic/uavcan/cz7UBGZTdF8 for how to get things working on Win
# thx, Pavel !

import uavcan, time, math
import msvcrt, sys
import matplotlib.pyplot as plt
import numpy as np
from scipy.optimize import curve_fit


# class to record data in repeated up/down sweeps
cSTATUS_INITIALIZEMOTOR = 0
cSTATUS_INITIALRAMP = 1
cSTATUS_RECORDINGRAMP = 2
cSTATUS_ABORTRAMP = 3
cSTATUS_EXIT = 4

class cRecord:

    def __init__(self,_node,_escIndex,_fig=None,_ax=None,_ax2=None):
        self.node = _node
        self.escIndex = _escIndex
        
        self.status = cSTATUS_INITIALIZEMOTOR
        self.status_cnt = 20 #startup initialization time, 1 sec
        self.setpoint = int(0)
        self.direction_up = True
        
        if self.escIndex > 3:
            self.emptyCommands = [0]*(self.escIndex+1) #this adapts to the number of ESCs
        else:    
            self.emptyCommands = [0,0,0,0] #assume at minimum 4 ESCs
            
        self.pwm = []    
        self.rpm = []    
        self.current = []    
        self.fig = _fig
        self.ax = _ax
        self.ax2 = _ax2

    def broadcastEscSetpoint(self):
        if self.status == cSTATUS_INITIALIZEMOTOR:
            self.setpoint = int(0)
            self.status_cnt -= 1
            if self.status_cnt <= 0: 
                self.direction_up = True
                self.status = cSTATUS_INITIALRAMP #cSTATUS_RECORDINGRAMP
        elif self.status == cSTATUS_INITIALRAMP:
            if self.direction_up:
                self.setpoint += 20 
                if self.setpoint >= 1500: self.direction_up = False
            else:
                self.setpoint -= 20
                if self.setpoint <= 100: 
                    self.direction_up = True
                    self.status = cSTATUS_RECORDINGRAMP
        elif self.status == cSTATUS_RECORDINGRAMP or self.status == cSTATUS_ABORTRAMP:
            if self.direction_up:
                self.setpoint += 20 
                if self.setpoint >= 8100: self.direction_up = False
            else:
                self.setpoint -= 20
                if self.setpoint <= 100: self.direction_up = True
            if self.status == cSTATUS_ABORTRAMP:
                self.direction_up = False # 'quick' abort, comment out to have complete sweeps
                if self.setpoint <= 101:
                    self.setpoint = int(0)
                    self.status = cSTATUS_EXIT
    
        commands = self.emptyCommands
        commands[self.escIndex] = self.setpoint
        message = uavcan.equipment.esc.RawCommand(cmd=commands)
        self.node.broadcast(message)
    
    def printEscStatus(self,msg):
        if self.status >= cSTATUS_RECORDINGRAMP and not math.isnan(msg.message.rpm) and not math.isnan(msg.message.current):
            self.pwm.append(self.setpoint)
            self.rpm.append(msg.message.rpm)
            self.current.append(msg.message.current)
            
        if self.status >= cSTATUS_ABORTRAMP:
            print('  ',self.setpoint,', ',msg.message.rpm,'rpm, ',msg.message.current,'A','STOP')
        else:
            print('  ',self.setpoint,', ',msg.message.rpm,'rpm, ',msg.message.current,'A')
            
        if self.fig:
            self.ax.clear()
            self.ax.plot(self.pwm,self.rpm,'bo')
            self.ax2.clear()
            self.ax2.plot(self.pwm,self.current,'r')
            self.fig.canvas.draw()
            time.sleep(0.01)
        #print(uavcan.to_yaml(msg))
        
    def run(self):
        hPeriodic = self.node.periodic(0.05, self.broadcastEscSetpoint)
        hEscStatus = self.node.add_handler(uavcan.equipment.esc.Status, self.printEscStatus)
        while self.status < cSTATUS_EXIT:
            try:
                self.node.spin(1)
                if msvcrt.kbhit():
                    msvcrt.getch()
                    self.status = cSTATUS_ABORTRAMP
            #except UAVCANException as ex: #leads to NameError: name is not defined ???
            #    print('NODE ERROR:', ex)            
            except KeyboardInterrupt:
                sys.exit(0)
        hEscStatus.remove()
        hPeriodic.remove()

        
def createFig0():
    #plt.ion()
    fig0 = plt.figure(0)
    
    ax01 = fig0.add_subplot(111)
    ax01.plot([], [], 'bo')
    ax01.set_xlabel('pwm') #doesn't work, why?
    ax01.set_ylabel('rpm') #doesn't work, why?
    ax01.tick_params( axis='y', colors='b' )
    ax01.relim() 
    ax01.autoscale_view(True,True,True)
    
    ax02 = ax01.twinx()
    ax02.plot([], [], 'r')
    ax02.set_ylabel('current (A)') #doesn't work, why?
    ax02.tick_params( axis='y', colors='r' )
    ax02.relim() 
    ax02.autoscale_view(True,True,True)
    
    fig0.tight_layout()
    fig0.canvas.draw()
    
    return fig0, ax01, ax02


'''
Theory:
    Prop:
    S = c_S rho omega^2 D^4
    P_M = c_P rho omega^3 D^5
    P_M = M omega
    => 
    S^3 = pi/2 rho D^2 xi^2 P_M^2
    
    Motor:
    M \approx k I
    =>
    S^3 \approx pi/2 rho D^2 xi^2 k^2 I^2 omega^2 = c^3 (I omega)^2
    =>
    S(pwm) \approx c [I(pwm) omega(pwm)]^(2/3)
'''
def calculateThrust(record):
    pwm_scaled = []
    thrust = []
    for i in range(len(record.pwm)):
        pwm = record.pwm[i]
        pwm_scaled.append( pwm/8192.0 )
        current = record.current[i]
        omega = record.rpm[i] #we don't ned to convert to proper units, since only the exponent in the algebraic function is relevant
        thrust.append( math.pow(current*omega,2.0/3.0) )
        
    return pwm_scaled, thrust

    
def createFig1(pwm_scaled,thrust):
    fig1 = plt.figure(1)
    ax11 = fig1.add_subplot(111)
    ax11.plot( pwm_scaled, thrust, 'bo')
    ax11.plot( pwm_scaled, thrust, 'b')
    ax11.set_xlabel('scaled pwm')
    ax11.set_ylabel('estimated thrust (a.u.)')    
    
    fig1.canvas.draw()
    
    
def calculateNormalizedThrustCurve(_pwm_scaled,_thrust,spin_min=0.15,spin_max=0.95):
    pwm_norm = []
    thrust_norm = []
    thrust_max = 0.0
    thrust_min = 1.0e10
    for i in range(len(_pwm_scaled)):
        pwm = _pwm_scaled[i]
        if (pwm < spin_min) or (pwm > spin_max): continue #only search in the allowed range
        thrust = _thrust[i]
        if thrust > thrust_max: thrust_max = thrust
        if thrust < thrust_min: thrust_min = thrust
    
    for i in range(len(_pwm_scaled)):
        pwm = _pwm_scaled[i]
        if (pwm < spin_min) or (pwm > spin_max): continue #only accept the allowed range
        pwm_n = pwm # is identical to scaled pwm
        pwm_norm.append( pwm_n )
        thrust = _thrust[i]
        thrust_n = (thrust - thrust_min)/(thrust_max - thrust_min) #must be ranged such that it 0,1 at MOT_SPIN_MIN,MOT_SPIN_MAX
        thrust_norm.append( thrust_n )
        
    return pwm_norm, thrust_norm

    
def createFig23(pwm_norm,thrust_norm,fit=None):
    if fit:
        fig = plt.figure(3)
    else:    
        fig = plt.figure(2)
    ax = fig.add_subplot(111)
    ax.plot( pwm_norm, thrust_norm, 'bo')
    ax.plot( pwm_norm, thrust_norm, 'b')
    ax.set_xlabel('normalzed pwm')
    ax.set_ylabel('normalized thrust')
    if fit:
        ax.plot( pwm_norm, fit, 'ro')
    ax.set_xlim([0.0,1.0])    
    ax.set_ylim([0.0,1.0])    
    fig.canvas.draw()
    
'''
Theory
    there is info here http://ardupilot.org/copter/docs/motor-thrust-scaling.html
    a more detailed account of what the current code in ArduCopter is doing,
    has been worked out here https://discuss.ardupilot.org/t/using-measured-mot-thst-expo-what-improvement-can-one-expect/26172/23
    
    The math doen in ArduCopter can be summarized as follows:
    // converts thrust_in = [0…1] to throttle_ratio = [0…1]
    throttle_ratio =
        [ -(1.0-expo) + sqrt{ (1.0-expo)*(1.0-expo) + 4.0 * expo * lift_max * thrust_in } ]
        /
        [ 2.0 * expo * batt_voltage_filt ]
    // converts throttle_ratio = [0…1] to X = [spin_min…spin_max]
    X = spin_min + (spin_max - spin_min) * throttle_ratio(thrust_in)
    // converts X = [0…1] to pwm = [pwm_min…pwm_max]
    thrust_to_pwm = pwm_min + (pwm_max - pwm_min) * X    
    =>
    X_norm = (X - spin_min) / (spin_max - spin_min)    
    thrust_in = (1-expo) * X_norm + expo * X_norm^2
'''

fitfunc_x_min = 0.0
fitfunc_x_max = 1.0

def setFitFuncMinMax(spin_min=0.15,spin_max=0.95):
    global fitfunc_x_min
    global fitfunc_x_max
    fitfunc_x_min = spin_min
    fitfunc_x_max = spin_max

def fitFunc(x, a):
    x_n = (x - fitfunc_x_min)/(fitfunc_x_max - fitfunc_x_min)
    return (1.0-a) * x_n + a * x_n*x_n
        

def fitNormalizedThurstCurve(pwm_norm,thrust_norm,_min, _max):
    '''
    thrust_norm = []
    for i in range(len(pwm_norm)): thrust_norm.append( func(pwm_norm[i],0.8) )        
    '''
    
    xdata = np.array(pwm_norm)
    ydata = np.array(thrust_norm)
    
    setFitFuncMinMax(_min, _max)
    
    popt, pcov = curve_fit(fitFunc, xdata, ydata, p0=(0.5))    
    return popt[0], pcov[0][0]
    
        
def createNode(com):
    node = uavcan.make_node(com, node_id=126, bitrate=1000000, baudrate=1000000)

    node_monitor = uavcan.app.node_monitor.NodeMonitor(node)

#    dynamic_node_id_allocator = uavcan.app.dynamic_node_id.CentralizedServer(node, node_monitor)
#    while len(dynamic_node_id_allocator.get_allocation_table()) <= 1:
#        print('Waiting for other nodes to become online...')
#        node.spin(timeout=1)
        
    while len(node_monitor.get_all_node_id()) < 1:
        print('Waiting for other nodes to become online...')
        node.spin(timeout=1)
        
    all_node_ids = list(node_monitor.get_all_node_id())
    print( '\nDetected Node IDs',all_node_ids)
    print( 'Node ID in use',all_node_ids[0],)
    node_dict = node_monitor.get(all_node_ids[0]) #momentarily, always use the first, one shouldk use an ESC detection scheme as in the examples
    
    return node;

    
if __name__ == '__main__':

    node = createNode('COM38');
    
    escIndex = 3

    print('\nsave files at end (y/n)?')
    saveFiles = False
    if msvcrt.getch() != 'n': saveFiles = True
    
    print('\nPress keyboard to START... ')
    while True:
        try:
            if msvcrt.kbhit():
                msvcrt.getche()
                break
        except KeyboardInterrupt:
            sys.exit(0)

    print('\nSTART Data recording... ')
    fig0, ax01, ax02 = createFig0()
    plt.show(block=False)
    record = cRecord(node, escIndex, fig0, ax01, ax02) #enter the desired esc index
    record.run()
    print('DONE')

    if len(record.pwm) > 2:
        print('calculating thrust curve... ')
        pwm_scaled, thrust = calculateThrust(record)
        #createFig1(pwm_scaled, thrust)
        print('DONE')
        
        MOT_SPIN_MIN = 0.15
        MOT_SPIN_MAX = 0.95
        
        print('calculating normalized thrust curve... ')
        pwm_norm, thrust_norm = calculateNormalizedThrustCurve(pwm_scaled, thrust, MOT_SPIN_MIN, MOT_SPIN_MAX)
        createFig23(pwm_norm, thrust_norm)
        print('DONE')
        
        print('fitting normalized thrust curve... ')
        popt, pcov = fitNormalizedThurstCurve(pwm_norm, thrust_norm, MOT_SPIN_MIN, MOT_SPIN_MAX) #       popt, pcov = 0.5,0.0
        print(popt,pcov)
        fit = []
        for i in range(len(pwm_norm)): fit.append( fitFunc(pwm_norm[i],popt) )        
        createFig23(pwm_norm, thrust_norm, fit)
        print('DONE')
                
        if saveFiles:
            fname = 'esc-thr-curve.'+str(escIndex)
            F = open( fname+'.raw.dat', 'w')
            F.write( 'i\tpwm\tpwm_scaled\trpm\tcurrent\tthrust\n' )
            for i in range(len(record.pwm)):
                line = ''
                line += str(i) + '\t'
                line += str(record.pwm[i]) + '\t'
                line += '{:.6f}'.format(pwm_scaled[i]) + '\t'
                line += '{:.6f}'.format(record.rpm[i]) + '\t'
                line += '{:.6f}'.format(record.current[i]) + '\t'
                line += '{:.6f}'.format(thrust[i]) + '\n'
                F.write( line )
            F.close()
    
            F = open( fname+'.normalized.dat', 'w')
            F.write( 'i\tpwm_norm\tthrust_norm\tfit\n' )
            for i in range(len(pwm_norm)):
                line = ''
                line += str(i) + '\t'
                line += '{:.6f}'.format(pwm_norm[i]) + '\t'
                line += '{:.6f}'.format(thrust_norm[i]) + '\t'
                line += '{:.6f}'.format(fit[i]) + '\n'
                F.write( line )
            F.close()
    
    plt.show(block=True)
    

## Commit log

2017-11-16 release uc4h esc actuator node v002
2017-11-17 release uc4h esc actuator node v003
2018-01-14 esc-actuator v004
2018-02-06 release esc actuator v006
2018-02-09 release uc4h esc v008
2018-02-18 release uc4h esc v009 and uc4h notify v002
2018-02-21 release UC4H ESC KISS and Mini Eagle layouts
    [uc4h esc kiss v100.brd, uc4h esc kiss v100.sch, uc4h esc mini v100.brd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]
2018-02-23 group order stuff added
    [UC4H-ESC-KISS-v100-BOM-sz2u.xls, uc4h esc kiss v100.brd, uc4h esc kiss v100.sch]
2018-02-25 release esc v0.10 notify v0.03
2018-02-27 esc thrust curve .py
2018-02-28 esc thr curve script improved
2018-02-28 esc thr curve script updated
2018-03-03 uc4h esc setup py script v001
2018-03-26 release uc4h-esc v011 and esc_setup v002
2018-03-31 release bootloader-v003, updated esc v012, notify v004
2018-03-31 release uc4h-esc v013
2018-04-04 release uc4h-esc v014
2018-07-15 release uartbridge v002 firmwares
2018-07-19 release uartbridge v003 firmware
2018-07-22 release uartbridge v004 firmware
2018-08-02 release board uc4h node v2.0.10
    [uc4h node v2010.brd, uc4h node v2010.sch]
2018-08-17 release board uc4h air/airspeed v0.2.0
    [uc4h airspeed v020-wholes.brd, uc4h airspeed v020-wholes.sch]
2018-08-17 release esc actuator v016 firmware
2018-09-14 release UC4H SLCAN adapter v1.01 layout
    [uc4h slcan adapter v101.brd, uc4h slcan adapter v101.sch]
2018-09-14 release board UC4H Node v2.0.11
    [uc4h node v2010.brd, uc4h node v2010.sch, uc4h node v2011.brd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]
2018-09-27 release board UC4H Node v2.1.00
    [uc4h node v2011.brd, uc4h node v2011.sch, uc4h node v2100.brd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]
2018-09-29 release firmware esc-actuator v017
2018-09-29 release firmware uartbridge v005
    dynamic node allocation, setup shortname
2018-09-29 release firmware esc-actuator v017
    dynamic node id allocation, setup shortname
2018-11-01 release olliw's parameters
    [olliws-20181101-flamewheel-v2.param]
2018-11-10 release uc4 escactuator firmware v0.20
    bug in temperature, wasn't converted for C to K
2018-12-02 release firmware esc-actuator v0.22
2018-12-08 UC4H Airpseed v0.401 pcb released
    [uc4h airspeed v020-wholes.brd, uc4h airspeed v020-wholes.sch, uc4h airspeed v0401 addonrscspi1.brd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]
2019-01-13 release mavlinkbridge v006, gpsmagbaro v027, powerbrick v010, betacopter v017u
2019-01-13 release powerbrick v010
2019-02-15 release RangeFinder v0.03, GpsMagBaro v0.28, UartBridge v0.08, Bootloader v0.07, BetaCopter 3.6.6-v018u
    [uc4h airspeed v020-wholes.brd, uc4h airspeed v020-wholes.sch, uc4h airspeed v0401 addonrscspi1.brd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]
2019-02-15 release PCB UC4H RangeFinder TFMini Carrier
    [uc4h tfmini v0201.brd, uc4h tfmini v0201.sch]
2019-02-24 release PCB UC4H RangeFinder VL53Lxx v0.1.00
    [uc4h vl53lxx v0100.brd, uc4h vl53lxx v0100.sch]
2019-04-06 release UC4H Cube Carrier v0.3 pcb
    [uc4h cube carrier v0310r-imx.brd, uc4h cube carrier v0310r-imx.sch, uc4h cube carrier v0310r.brd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]
2019-04-06 release UC4H GpsMagBaroLed Carrier v0.3 pcb
    [uc4h gpsmagbaro v0301.brd, uc4h gpsmagbaro v0301.sch, uc4h gpsmagbaro ws2812 v0100.brd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]
2019-04-06 move up UC4H Airspeed v0.4 pcb
    [uc4h airspeed v020-wholes.brd, uc4h airspeed v020-wholes.sch, uc4h airspeed v0401 addonrscspi1.brd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]
2019-04-06 release firmware powerbrick v0.11

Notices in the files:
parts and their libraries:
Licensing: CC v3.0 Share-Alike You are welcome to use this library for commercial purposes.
